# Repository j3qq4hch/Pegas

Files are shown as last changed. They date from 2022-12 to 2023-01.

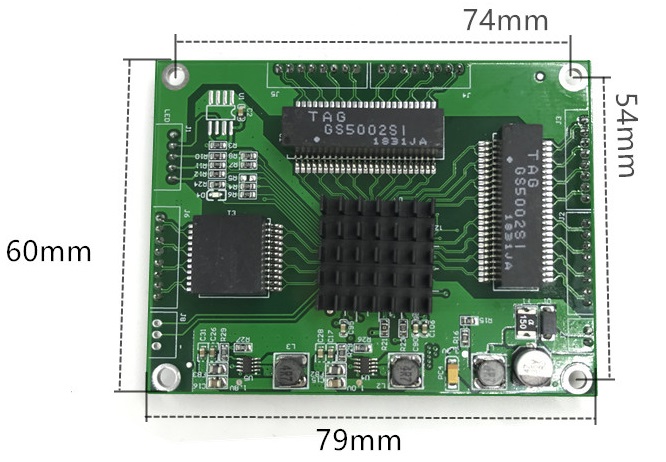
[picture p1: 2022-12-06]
figures/hub5port.jpg

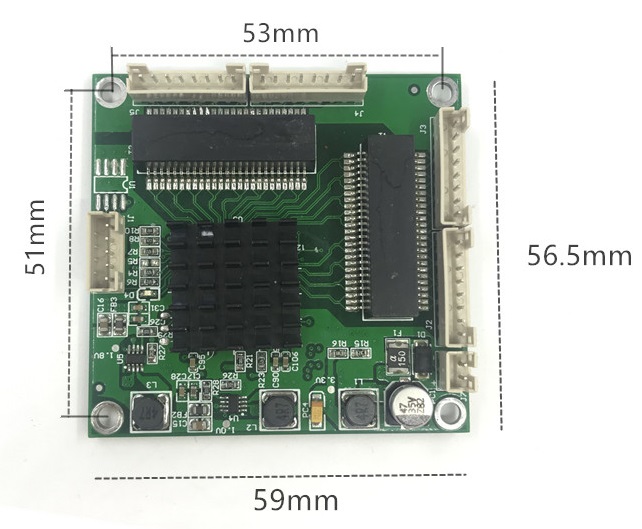
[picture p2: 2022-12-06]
figures/hub4port.jpg

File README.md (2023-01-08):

# Материнская плата БПЛА Pegas

Данный репозиторий содержит документацию и исходные файлы печатных плат электроники БПЛА Пегас.
Набортная электроника представляет собой главным образом материнскую плату (одну или набор из двух), которая служит для распределения питания внутри дрона, а также предоставляет интерфейс для подключения внешних устройств к автопилоту (удобные в производстве и использовании разъемы в удобных местах). БПЛА Пегас использует PX4-совместимый автопилот Cube Orange, которому всегда требуется некая материнская плата (carrier board в репозитории самого автопилота), т.к. он подключается ко всем внешним устройствам разъемом Hirose DF17(1.0H)-80DP-0.5V(57).

Было спроектировано несколько итераций электроники БПЛА Пегас.
## V1 
Самая первая версия устройства, состоящая из одной четырехслойной печатной платы.
Было произведен только один прототип, после чего была спроектирована следующая версия.

## V2
Минимальные отличия от V1, в частности: иная ориентация Cube Orange на плате (он повернут на 60 градусов), что было вызвано багом с устновлением нулевого положения встроенного компаса в ПО PX4, также добавлена схема выключения устройства на N-канальных полевых транзисторах. Схема выключения в этой версии неработоспособна и никогда не была исправлена. 

Также эта версия может быть дополнена внешним ethernet-роутером, который монтируется внутри фюзеляжа БПЛА на специальном кронштейне.

Было спроектировано две платы переходника для покупных модулей роутеров:

Было произведено несколько плат (до 10), которые используются в первых коммерческих аппаратах.

## V3
Полностью переработанная версия электроники: одна четырехслойная материнская плата  заменена на две двухслойные, соединенные мезонинным способом. Снизу располагается силовая плата, на которой размещаются разъемы для подключения моторов, медные полигоны распреления силового питания, DC-DC преобразователи всех вторичных линий питания, а также схема выключения на N-канальных полевых транзисторах. Сверху располагается плата логики с автопилотом и всеми разъемами для подключения внешних устройств. В этой версии произошел переход с миниатюрных разъемов серии JST-GH (как в UAVCAN) на несколько более крупные и значительно более удобные и надежные разъемы JST-XA с защелкой. 

Этот вариант материнской платы предназначен для сборки СЫЧ-версии Пегаса, поэтому помимо типичных компонентов на плате логики также располагается располагается покупной модуль ethernet-концентратора (ссылка тут) и модем телеметрии, поставляемый заказчиком (картинка тут).

Эта версия электроники никогда не была произведена и послужила основой для версии 3.1.

## V3.1

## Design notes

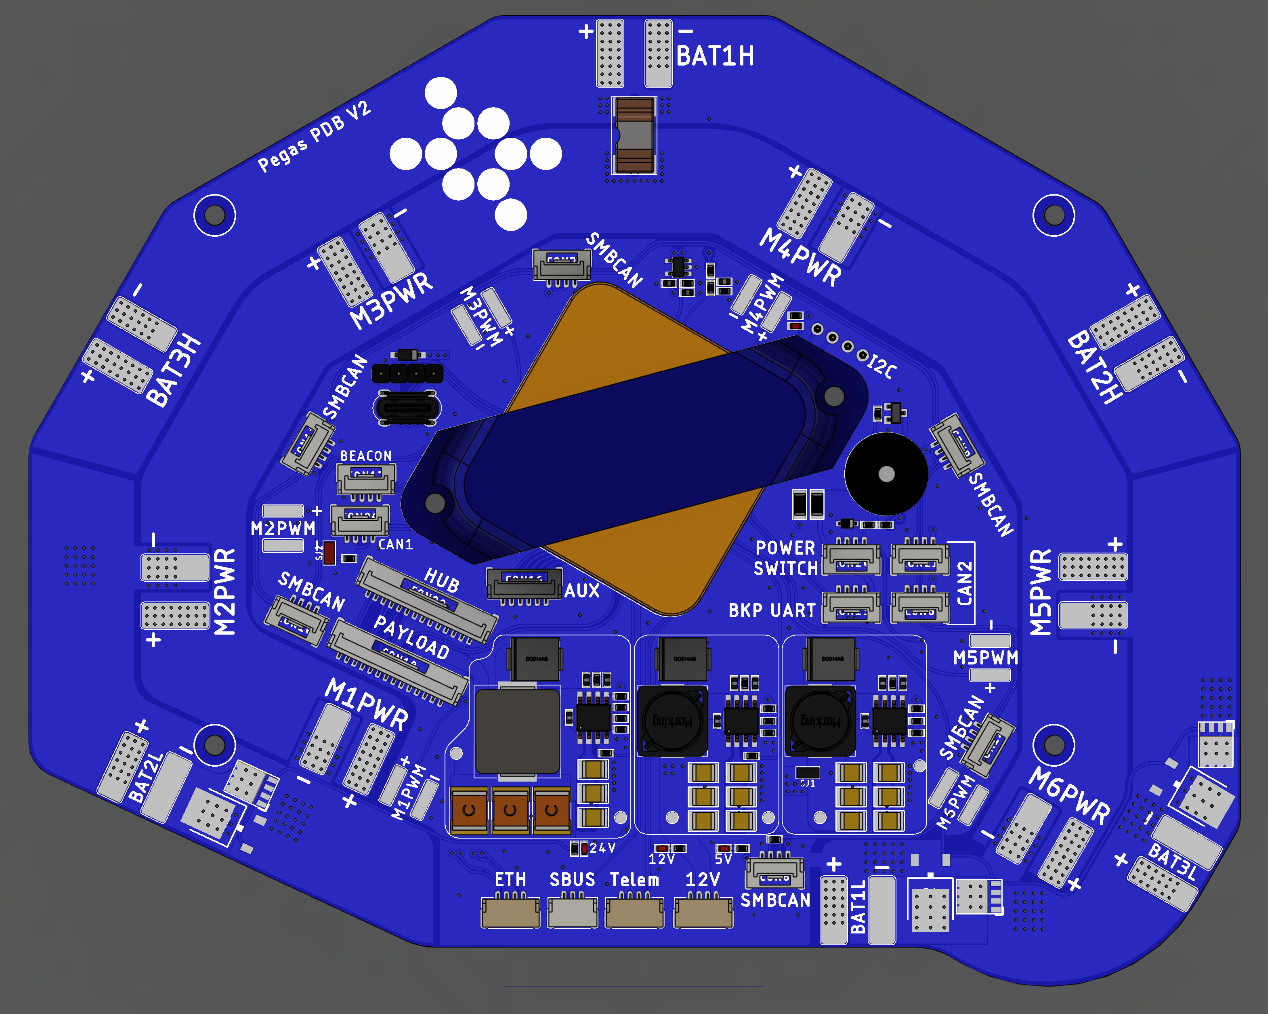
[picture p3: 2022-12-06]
figures/overview.png

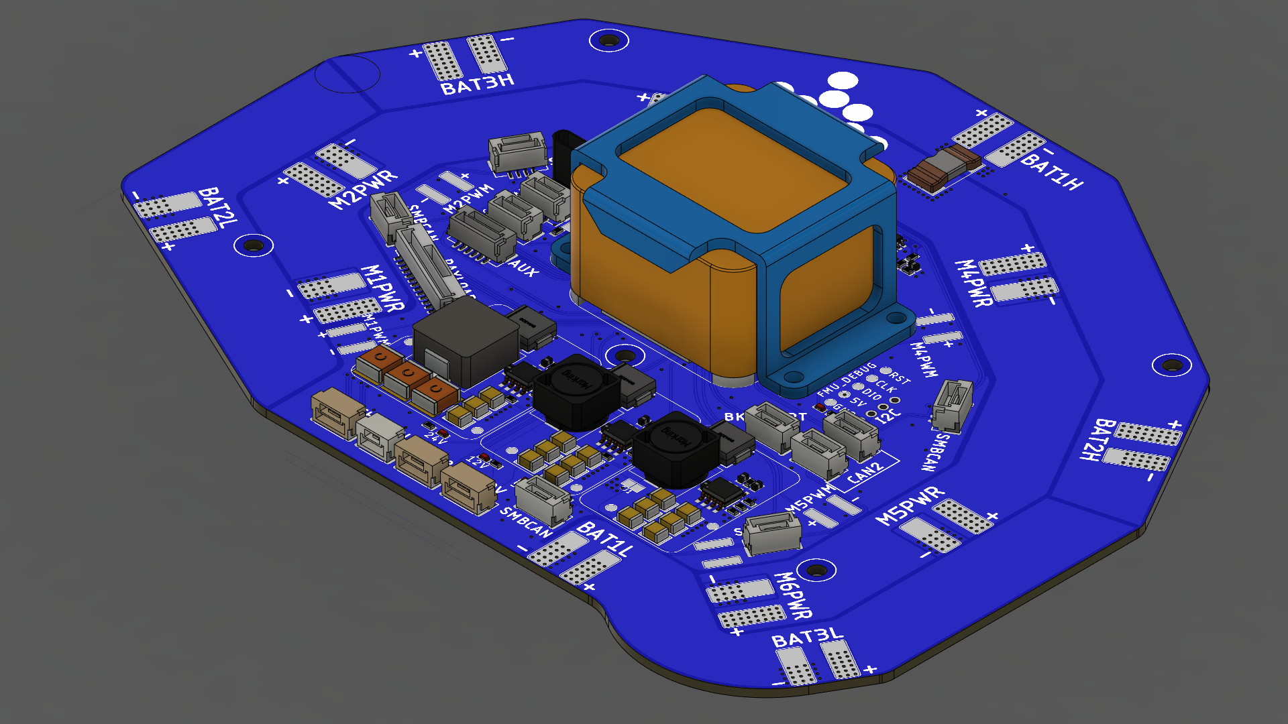
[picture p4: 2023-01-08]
figures/V1_overview.png

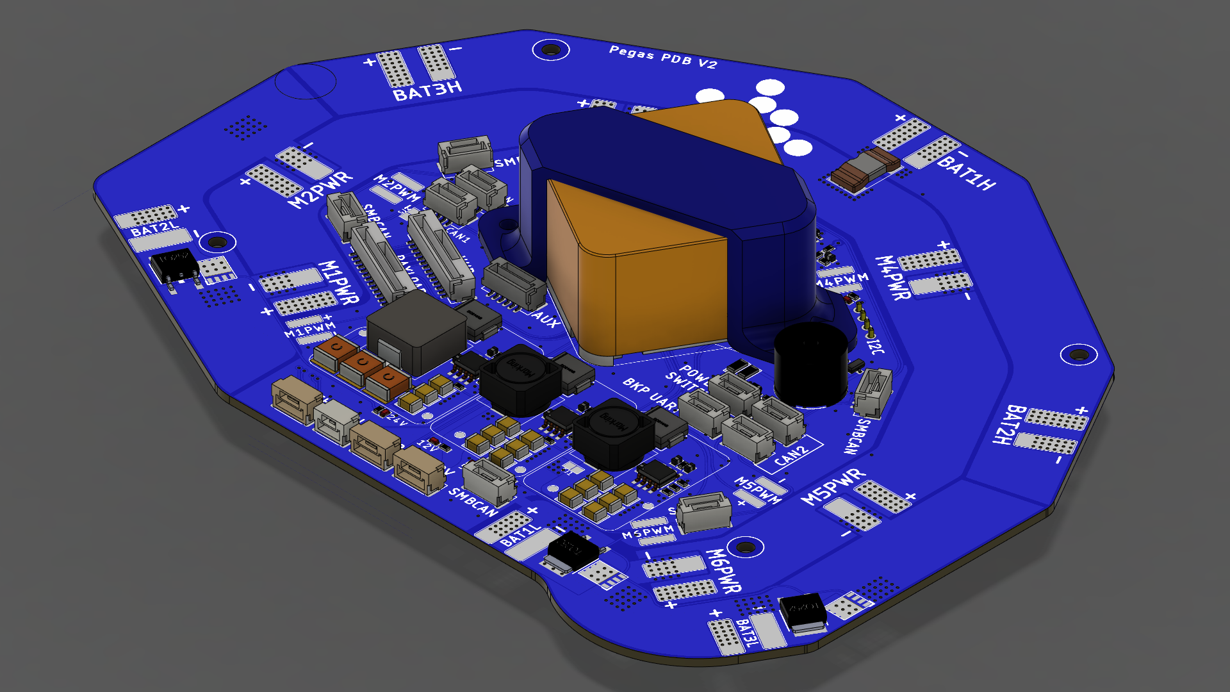
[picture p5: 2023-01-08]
figures/V2_overview.png

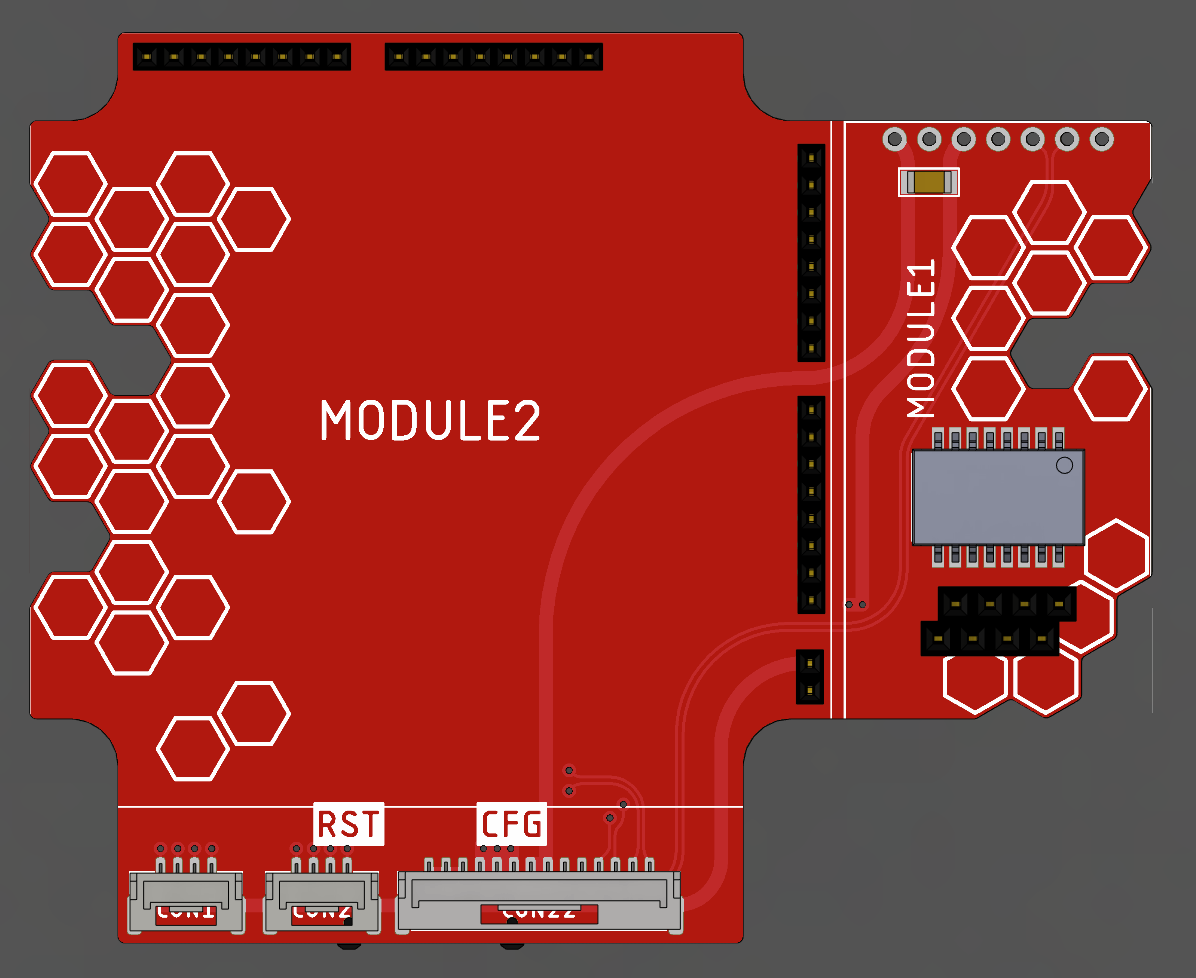
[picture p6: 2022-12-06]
figures/Hub4port_top.png

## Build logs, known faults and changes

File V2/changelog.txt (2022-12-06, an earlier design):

-Исправлено посадочное место USB разъема 
-Исправлена шелкография подключения ШИМ сигнала мотора 6
-Пин VDD_BRICK_VALID подключен к земле
-Полетный контроллер развернут на 60 градусов по часовой стрелки из-за несовершенства ПО PX4
-Изменено расположение последовательных интерфейсов(SERIAL1->CON4, SERIAL5->CON13, SERIAL5->CON17)
-Добавлен разъем для платы хаба

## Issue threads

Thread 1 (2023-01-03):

Ошибки BOM листа релиза 3.1

airPixel, 2023-01-03:
в релизном боме платы логики не попало все что стоит под свитчем, т.е. трансформаторы, дсдс и его обвязка, HLK-7788A

j3qq4hch, 2023-01-03:
Это не ошибка, это вариант сборки СЫЧ. Нельзя устанавливать эти трансформаторы если используется отдельный модуль свитча

airPixel, 2023-01-03:
а, ну ок. просто сижу собираю заказ в элитане и увидел несостыковку. дсдс получается не нужен для свитча?

j3qq4hch, 2023-01-03:
На плате свитча есть свой собственный. Наш не нужен

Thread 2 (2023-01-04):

замены компонентов

airPixel, 2023-01-04:
L1 powerPCB - IHLP2020BZER3R3M01 на VLC5045T-3R3N
вроде подходит и есть в бОльшем колве на элтитане

j3qq4hch, 2023-01-04:
Давай-ка лучше обсуждать замены компонентов из-за доступности не здесь, я не хочу менять их в проекте. Зато мы можем добавить альтернативные колонки в BOM и там же в комментариях это обсудить, если требуется.

airPixel, 2023-01-04:
давай тогда делать BOM всегда в гуглодоках( в этот раз только табличка была в экселе), и там тогда отдельный столбец с заменой. вполне вариант) только нужны права на изменения этого столбца

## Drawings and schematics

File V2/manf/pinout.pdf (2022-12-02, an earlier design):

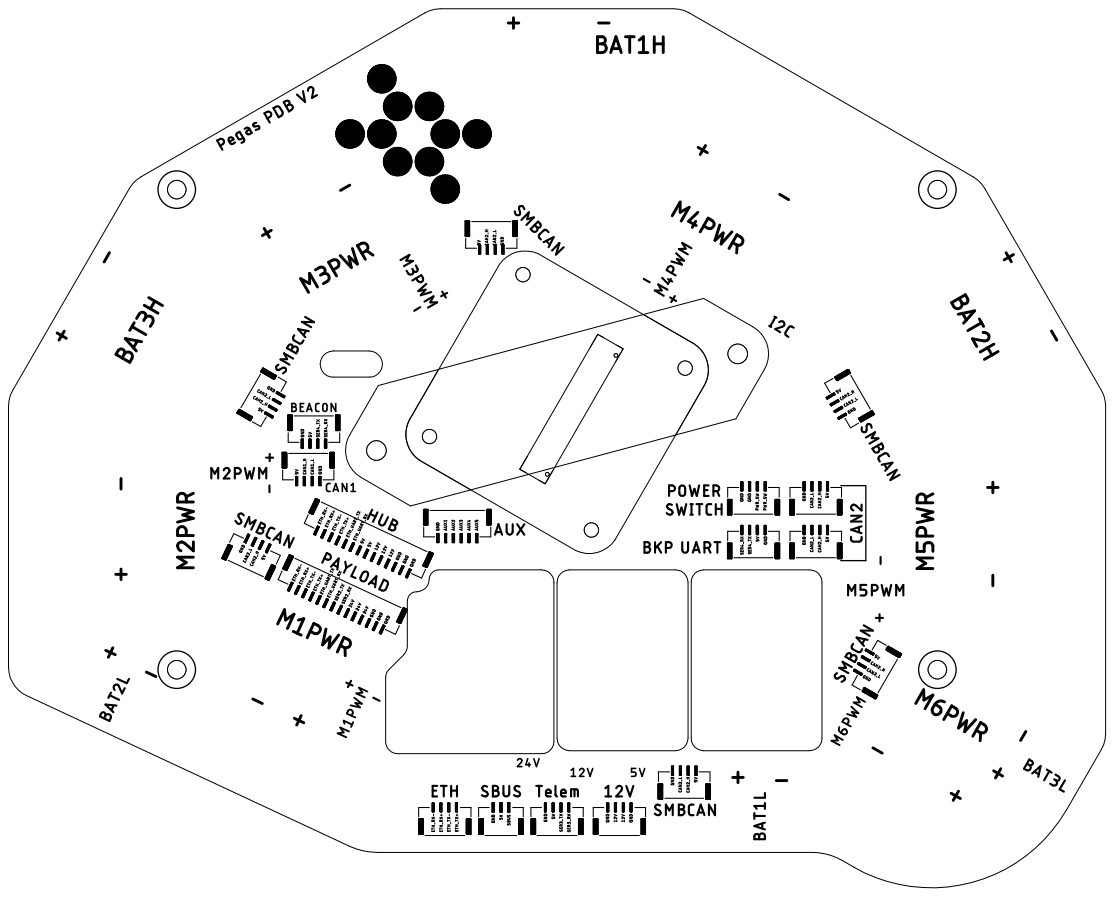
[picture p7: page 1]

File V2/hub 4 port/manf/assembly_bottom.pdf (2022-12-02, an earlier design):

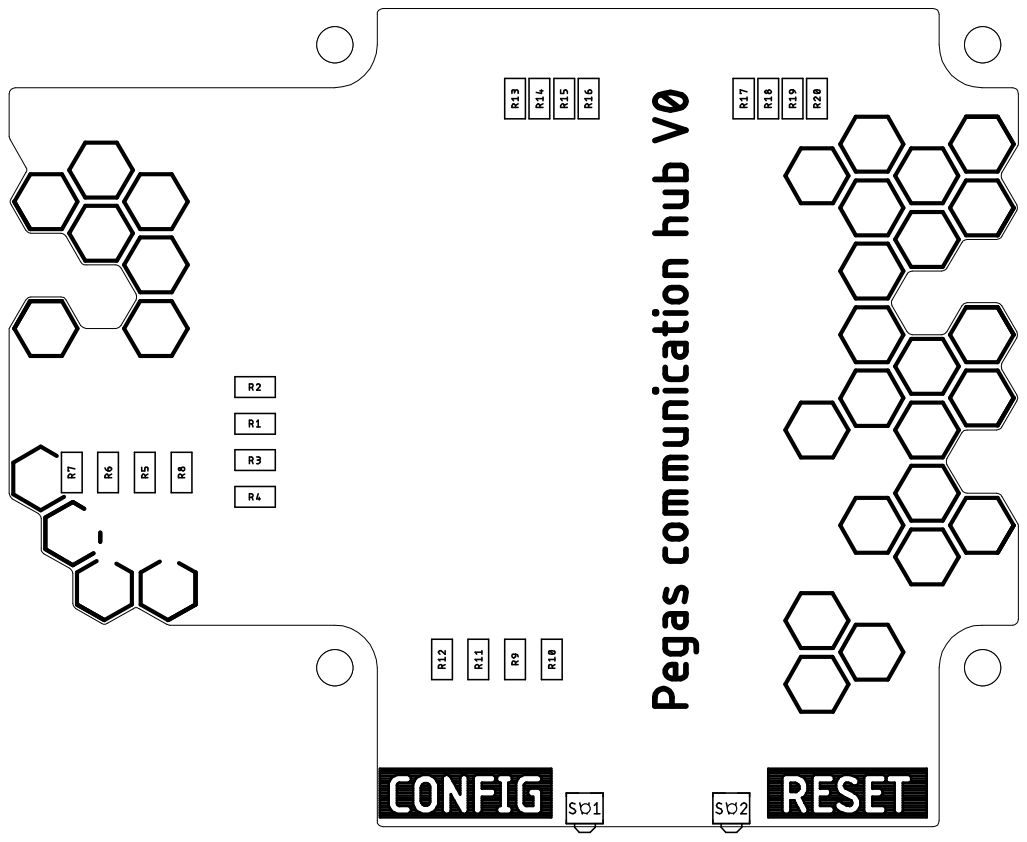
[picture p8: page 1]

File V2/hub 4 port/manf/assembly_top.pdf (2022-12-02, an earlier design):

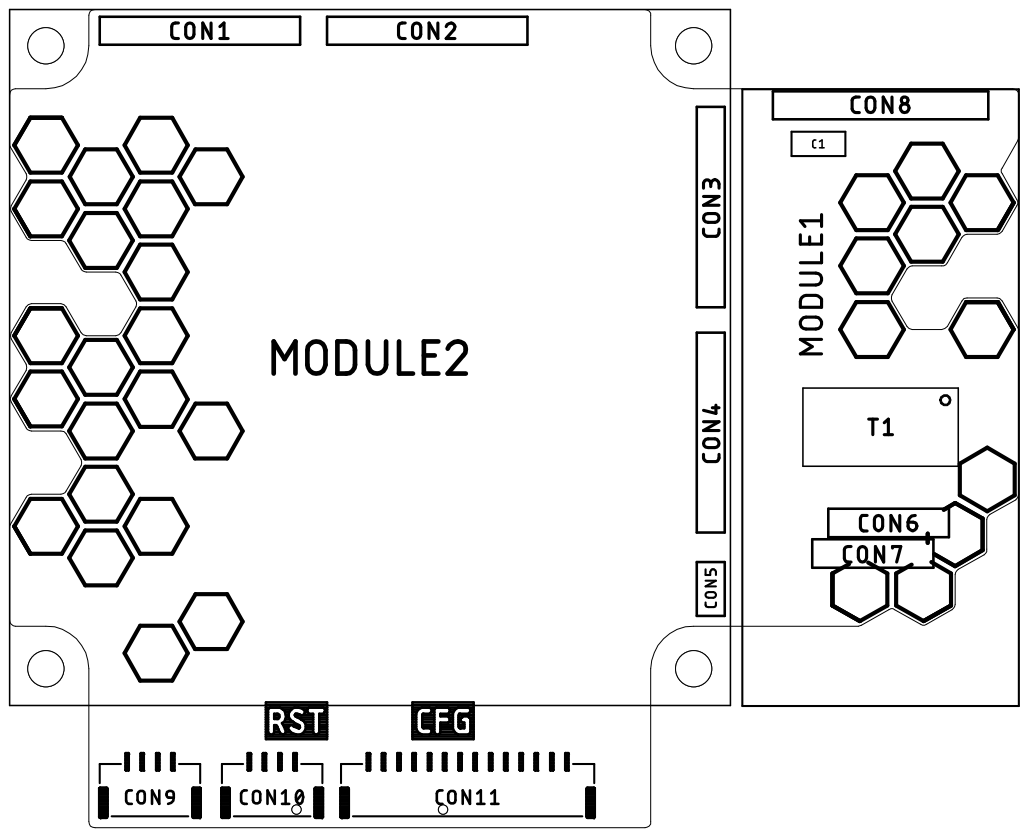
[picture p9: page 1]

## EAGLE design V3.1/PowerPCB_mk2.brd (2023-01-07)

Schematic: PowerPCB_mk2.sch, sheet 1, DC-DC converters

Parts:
C1, C10, C16, C25, C39, C58: 0.1u; C0603; VOLTAGE 50V; LCSC# C14663
C2, C3, C4, C11, C12, C13, C17, C18, C19, C26, C27, C33, C44, C54: 2.2u; C1206; VOLTAGE 100V; LCSC# C170101
C5, C14, C20, C34, C45, C62, C88: 4700p; C0603; VOLTAGE 50V; LCSC# C106218
C6, C15, C21, C35, C87: 47p; C0603; VOLTAGE 50V; LCSC# C1671
C7, C8, C9, C22, C23, C24, C36, C37, C38, C43, C56, C57: 47u; C1206; VOLTAGE 25V; LCSC# C403725
C28, C29, C30, C31, C32, C42: 10u; C1210; VOLTAGE 50V; LCSC# C77102
C40, C41: DNP; C0603
CON1: PINHEAD_1X12-2.54-FEMALE; 1X12-PTH-2.54-FEMALE
CON2, CON4, CON7: PINHEAD_1X06-2.54-FEMALE; 1X06-PTH-2.54-FEMALE
CON3: PINHEAD_1X02-2.54-FEMALE; 1X02-PTH-2.54-FEMALE
D1, D2, D3, D4, D10: B560C; DO-214AB(SMC)
IC1, IC2, IC3, IC4: TPS54560B; SOIC8-POWERPAD
IC5: INA169; SOT23-5
IC10: TPS54260; MSOP10; DIGIKEY# 296-28183-1-ND
J1: CONNECTION-7MM; CONNECTION_7MM
L1: 3.3uH; IHLP-2020BZ-01; LCSC# C844988
L2, L4, L5: 7.2uH; 1064
L3: 22µH; SRP1265A
Q1: IRLML9301; SOT23
R1, R5, R9, R13: 243K; R0603; LCSC# C23351
R2, R6, R10, R14, R22, R29: 18K; R0603; LCSC# C25810
R3, R11: 53K6; R0603; LCSC# C23074
R4, R8, R12, R16, R17, R20, R23, R28: 10K; R0603; LCSC# C160601
R7, R15, R21, R25: 143K; R0603; LCSC# C22877
R18, R26: 700 µOhms; R3920-KELVIN
R27: 39K; R0603; LCSC# C23153
RL: 53K6; R0603; LCSC# C23074
RL1: DNM; R0603; LCSC# C23153

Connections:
5VFMU: C7.P$2 (2), C8.P$2 (2), C9.P$2 (2), C39.2, IC5.5 (V+), L2.2, Q1.2 (S), R3.2, R23.1; also elsewhere on the board
5V_FMU_CTRL: Q1.1 (G), R23.2
BATNEG: CON3.1
BATT_CURRENT: C40.2, CON1.12, IC5.1 (OUT), RL.2, RL1.2
BATT_VOLTAGE: C41.2, CON1.11, R20.2, R22.1
BOOT: C58.2, IC10.1 (BOOT)
BOOT1: C1.1, IC1.1 (BOOT)
BOOT2: C16.1, IC3.1 (BOOT)
BOOT3: C25.1, IC4.1 (BOOT)
DC-DC_EN: IC2.3 (EN), IC3.3 (EN), IC4.3 (EN), IC10.3 (EN); also elsewhere on the board
GND: C2.P$1 (1), C3.P$1 (1), C4.P$1 (1), C5.1, C6.1, C7.P$1 (1), C8.P$1 (1), C9.P$1 (1), C11.P$1 (1), C12.P$1 (1), C13.P$1 (1), C14.1, C15.1, C17.P$1 (1), C18.P$1 (1), C19.P$1 (1), C20.1, C21.1, C22.P$1 (1), C23.P$1 (1), C24.P$1 (1), C26.P$1 (1), C27.P$1 (1), C28.1, C29.1, C30.1, C31.1, C32.1, C33.P$1 (1), C34.1, C35.1, C36.P$1 (1), C37.P$1 (1), C38.P$1 (1), C39.1, C40.1, C41.1, C42.1, C43.P$2 (2), C44.P$1 (1), C45.2, C54.P$1 (1), C56.P$2 (2), C57.P$2 (2), C62.2, C87.2, C88.2, CON1.1, CON1.2, CON1.5, CON1.6, CON1.7, CON2.1, CON2.2, CON2.3, CON4.4, CON4.5, CON4.6, CON7.4, CON7.5, CON7.6, D1.A, D2.A, D3.A, D4.A, D10.A, IC1.7 (GND), IC1.P$1 (GND), IC2.7 (GND), IC2.P$1 (GND), IC3.7 (GND), IC3.P$1 (GND), IC4.7 (GND), IC4.P$1 (GND), IC5.2 (GND), IC10.9 (GND), IC10.EP (GND), J1.2, R1.1, R4.1, R5.1, R8.1, R9.1, R12.1, R13.1, R16.1, R17.1, R20.1, R25.1, R28.1, RL.1, RL1.1; also elsewhere on the board
unnamed: IC1.4 (RT/CLK), R1.2
unnamed: IC3.4 (RT/CLK), R9.2
unnamed: C6.2, IC1.6 (COMP), R2.2
unnamed: C5.2, R2.1
unnamed: IC1.5 (FB), R3.1, R4.2
unnamed: C21.2, IC3.6 (COMP), R10.2
unnamed: C10.1, IC2.1 (BOOT)
unnamed: C10.2, D2.C, IC2.8 (SW), L3.1
unnamed: IC2.4 (RT/CLK), R5.2
unnamed: C15.2, IC2.6 (COMP), R6.2
unnamed: C14.2, R6.1
unnamed: IC2.5 (FB), R7.1, R8.2, R17.2
unnamed: C20.2, R10.1
unnamed: IC4.4 (RT/CLK), R13.2
unnamed: IC3.5 (FB), R11.1, R12.2
unnamed: C35.2, IC4.6 (COMP), R14.2
unnamed: C34.2, R14.1
unnamed: IC4.5 (FB), R15.1, R16.2
unnamed: IC5.4 (VIN-), R18.S2, R26.S2
unnamed: C45.1, C62.1, IC10.4 (SS/TR)
unnamed: IC5.3 (VIN+), R18.S1, R26.S1
unnamed: R21.1, R22.2
unnamed: CON1.8, CON1.9, CON1.10, Q1.3 (D)
unnamed: C87.1, IC10.8 (COMP), R29.2
unnamed: IC10.5 (RT/CLK), R25.2
unnamed: C88.1, R29.1
PGND: J1.1; also elsewhere on the board
PH: C58.1, D10.C, IC10.10 (PH), L1.P$1 (1)
PWRSW: CON3.2
SW1: C1.2, D1.C, IC1.8 (SW), L2.1
SW2: C16.2, D3.C, IC3.8 (SW), L4.1
SW3: C25.2, D4.C, IC4.8 (SW), L5.1
VBAT: C2.P$2 (2), C3.P$2 (2), C4.P$2 (2), C11.P$2 (2), C12.P$2 (2), C13.P$2 (2), C17.P$2 (2), C18.P$2 (2), C19.P$2 (2), C26.P$2 (2), C27.P$2 (2), C33.P$2 (2), C44.P$2 (2), C54.P$2 (2), IC1.2 (VIN), IC2.2 (VIN), IC3.2 (VIN), IC4.2 (VIN), IC10.2 (VIN), R18.2, R18.22 (2), R21.2, R26.2, R26.22 (2); also elsewhere on the board
VDC: R18.1, R18.11 (1), R26.1, R26.11 (1); also elsewhere on the board
VDD_4V: C43.P$1 (1), C56.P$1 (1), C57.P$1 (1), CON1.3, CON1.4, L1.P$2 (2), R27.2
VDD_5V: C22.P$2 (2), C23.P$2 (2), C24.P$2 (2), CON4.1, CON4.2, CON4.3, L4.2, R11.2
VDD_12V: C36.P$2 (2), C37.P$2 (2), C38.P$2 (2), CON7.1, CON7.2, CON7.3, L5.2, R15.2
VDD_24V: C28.2, C29.2, C30.2, C31.2, C32.2, C42.2, CON2.4, CON2.5, CON2.6, L3.2, R7.2
VSENSE: IC10.7 (VSENSE), R27.1, R28.2

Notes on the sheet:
24V power source
5V power source
When EN is left floating TPS54560 is enabled
12V power source
EN - Enable terminal, with internal pull-up current source. Pull below 1.2 V to disable. Float to enable.
EN PIN: Pull below 1.2 V to disable. Float to enable.
143K on RT/CLK is for ~800 KHz switching frequency
TPS54560/54260 Vout = 0.8 * (Rh/Rl + 1)
Vout = 3,92 V
Vout = 23,68 V
Vout = 12,24 V
Vout = 5.088
Place C3 in case low pass filtering on the output needed
For most applications, best performance is attained with an RS value that provides a full-scale shunt voltage of 50 mV to 100 mV; maximum input voltage for accurate measurements is 500 mV.
Imax = 169 A Vout max = 3.17 V

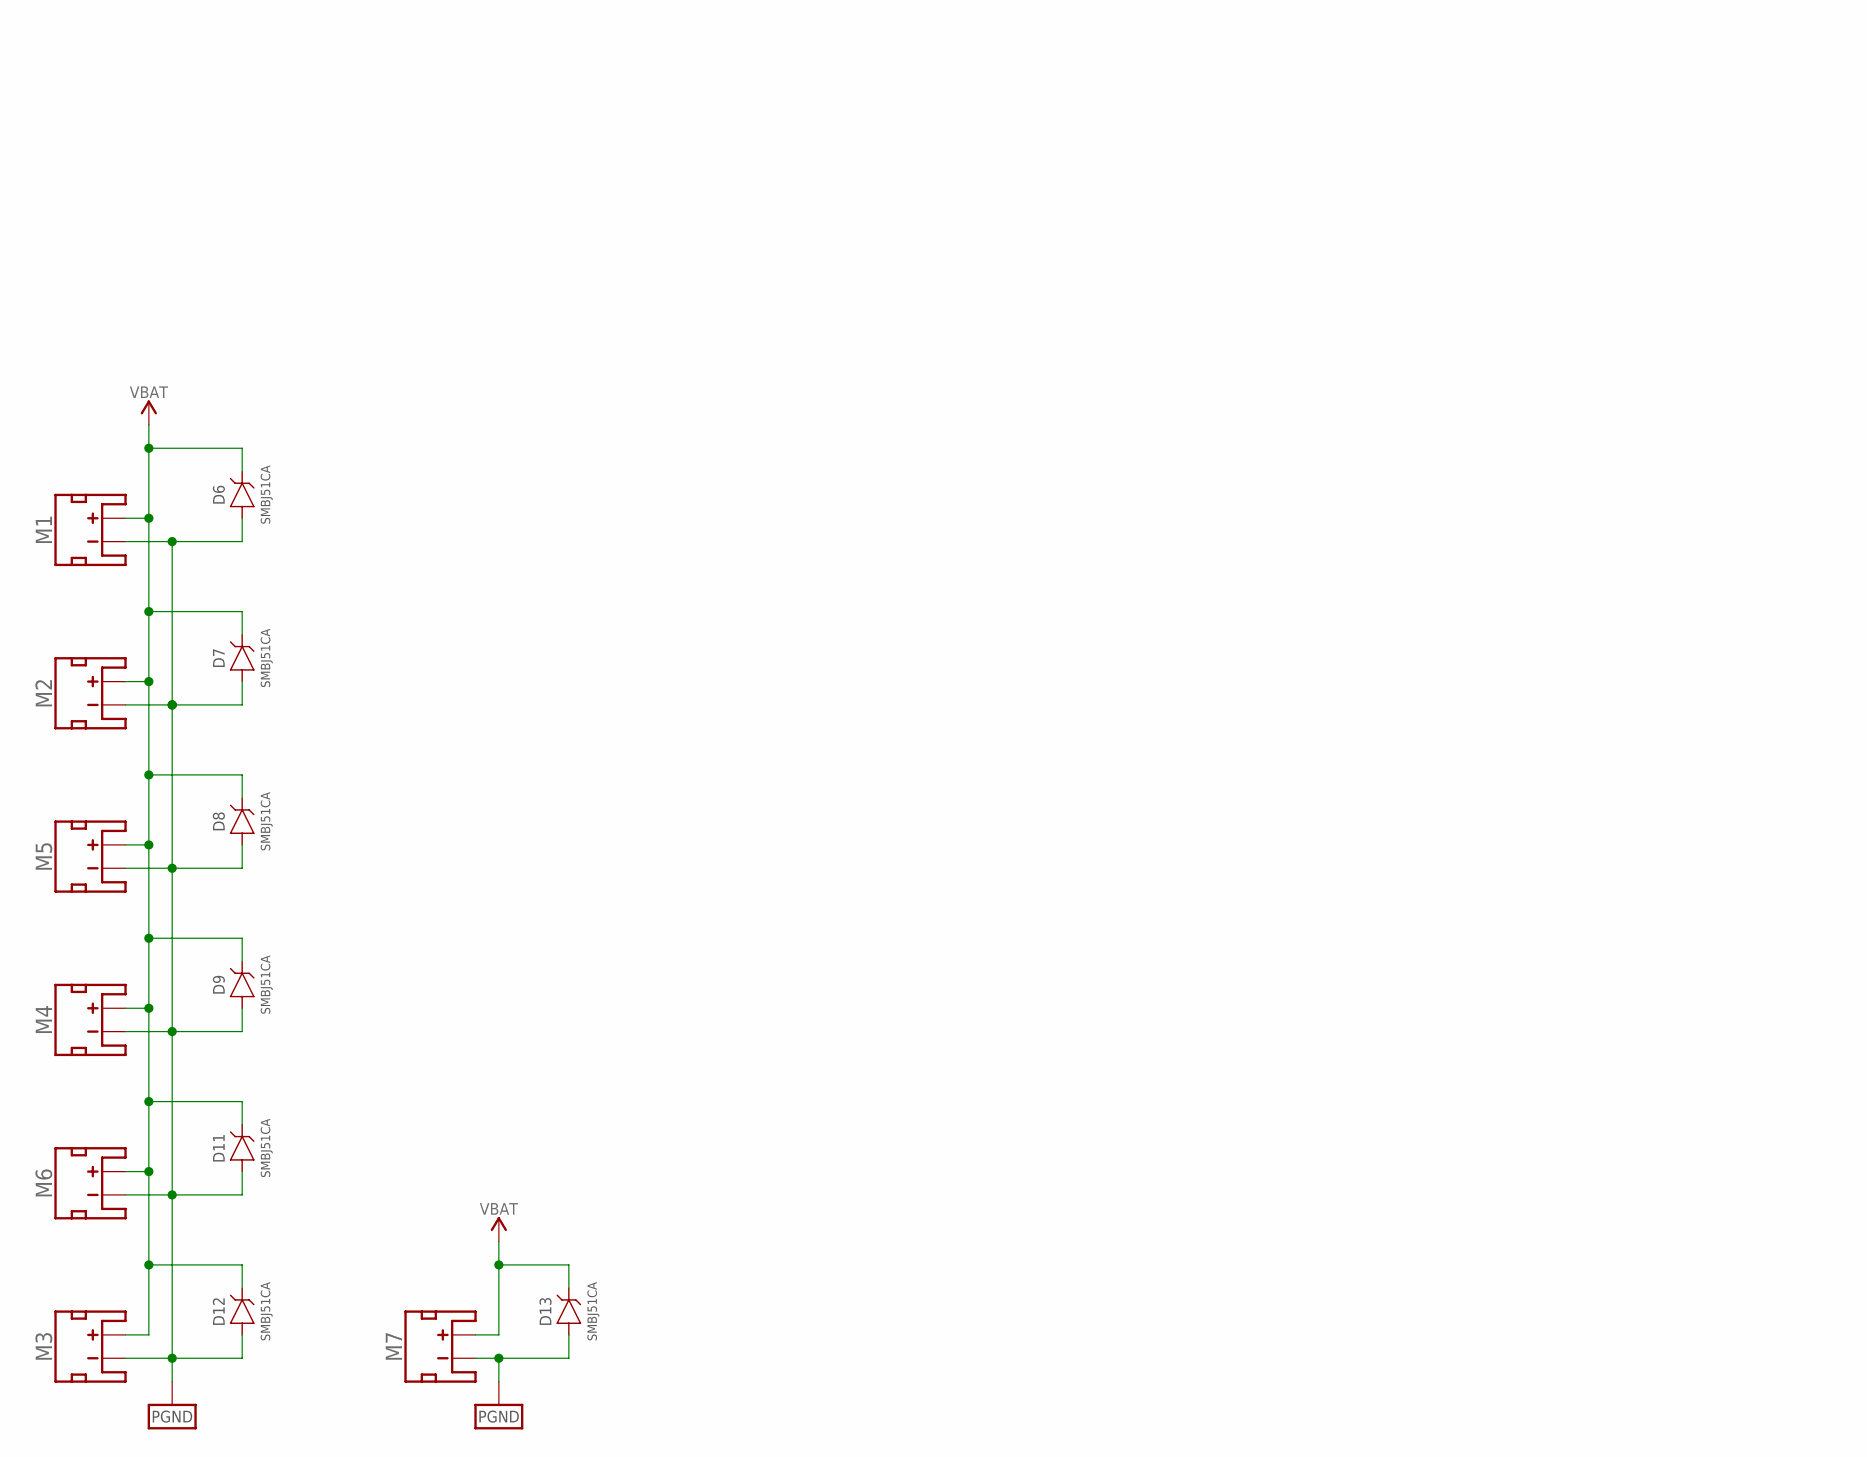
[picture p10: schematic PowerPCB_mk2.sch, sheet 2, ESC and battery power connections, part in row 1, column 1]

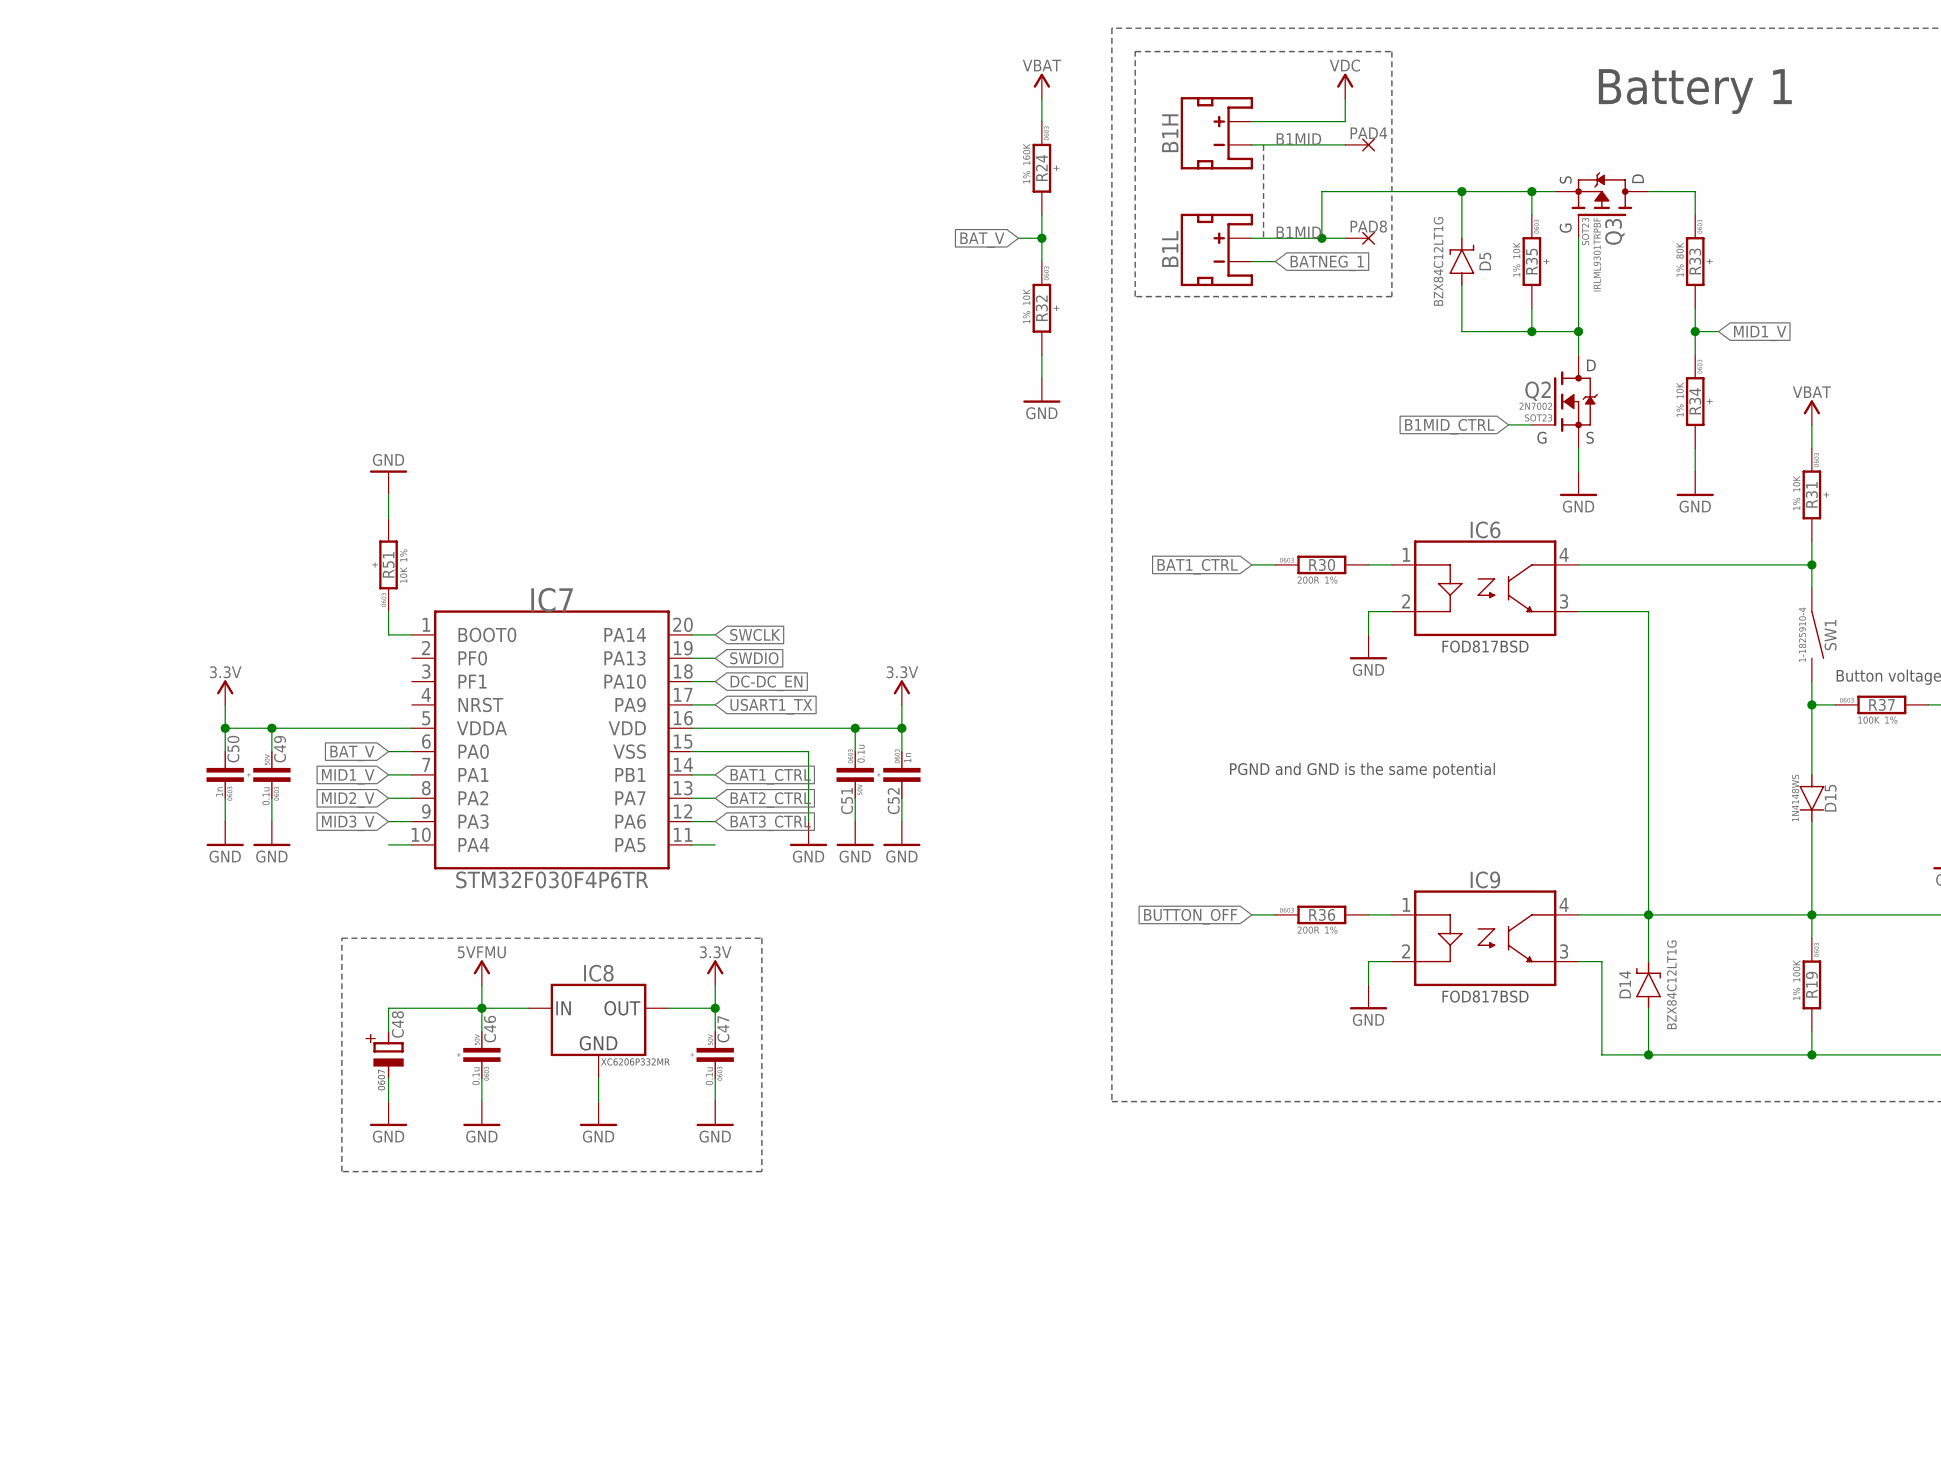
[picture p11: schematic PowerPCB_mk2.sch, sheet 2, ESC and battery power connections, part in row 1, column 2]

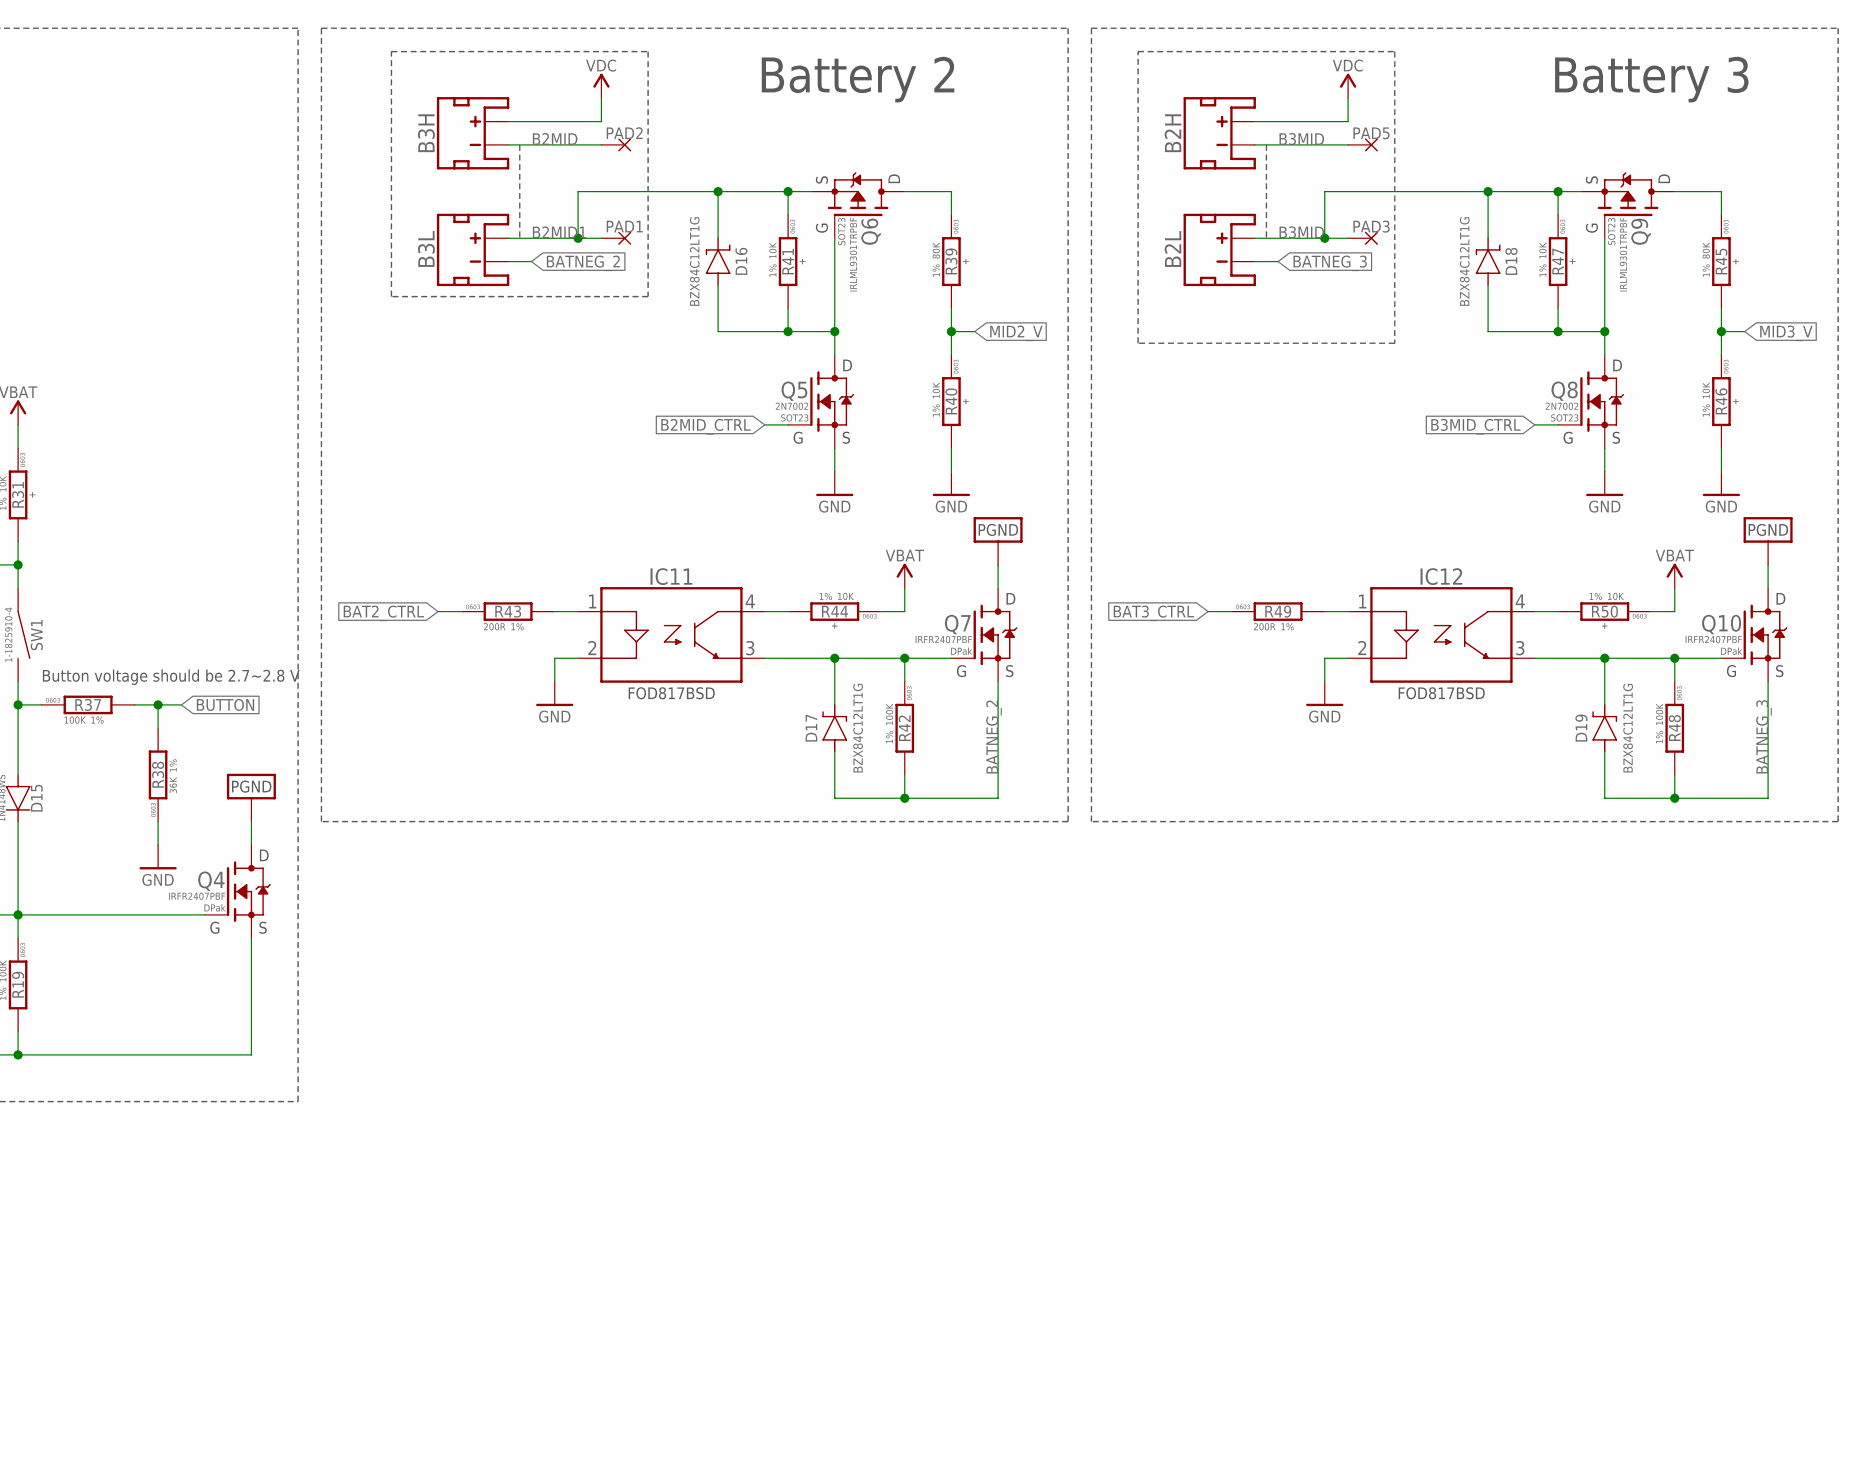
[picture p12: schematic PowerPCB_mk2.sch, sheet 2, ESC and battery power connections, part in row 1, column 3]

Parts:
B1H, B1L, B2H, B2L, B3H, B3L: BATTERY_CON-XT60PW-M; XT60PW-M
C46, C47, C49, C51: 0.1u; C0603; VOLTAGE 50V; LCSC# C14663
C48: CPOL-SMD_6.3X7.7; CAP_SMD_6.3X7.7
C50, C52: 1n; C0603
D5, D14, D16, D17, D18, D19: BZX84C12; SOT23
D6, D7, D8, D9, D11, D12, D13: SMBJ51CA-SMB; DO-214AA(SMB)
D15: 1N4148WS; SOD323
IC6, IC9, IC11, IC12: FOD817; 4-SMD
IC7: STM32F030F4P6; TSSOP20
IC8: XC6206P332MR; SOT23
M1, M2, M3, M4, M5, M6, M7: BATTERY_CON-XT30-RA; XT30-RA
PAD1, PAD2, PAD3, PAD4, PAD5, PAD8: PAD-10X4; 10X4
Q2, Q5, Q8: 2N7002; SOT23
Q3, Q6, Q9: IRLML9301; SOT23
Q4, Q7, Q10: IRFR2407PBF; D-PAK
R19, R37, R42, R48: 100K; R0603
R24: 160K; R0603; LCSC# C160601
R30, R36, R43, R49: 200R; R0603
R31, R32, R34, R35, R40, R41, R44, R46, R47, R50, R51: 10K; R0603; LCSC# C160601
R33, R39, R45: 80K; R0603; LCSC# C160601
R38: 36K; R0603
SW1: TACT_SWITCH-1-1825910-4; 1-1825910-4

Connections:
5VFMU: C46.2, C48.+, IC8.3 (IN); also elsewhere on the board
B1MID: B1H.-, B1L.+, D5.3 (C), PAD4.P$1, PAD8.P$1, Q3.2 (S), R35.1
B1MID_CTRL: Q2.1 (G)
B2MID: B3H.-, PAD2.P$1
B2MID1: B3L.+, D16.3 (C), PAD1.P$1, Q6.2 (S), R41.1
B2MID_CTRL: Q5.1 (G)
B3MID: B2H.-, B2L.+, D18.3 (C), PAD3.P$1, PAD5.P$1, Q9.2 (S), R47.1
B3MID_CTRL: Q8.1 (G)
BAT1_CTRL: IC7.14 (PB1), R30.1
BAT2_CTRL: IC7.13 (PA7), R43.1
BAT3_CTRL: IC7.12 (PA6), R49.1
BATNEG_1: B1L.-, D14.1 (A), IC9.3 (EMITTER), Q4.S, R19.2
BATNEG_2: B3L.-, D17.1 (A), Q7.S, R42.2
BATNEG_3: B2L.-, D19.1 (A), Q10.S, R48.2
BAT_V: IC7.6 (PA0), R24.2, R32.1
BUTTON: R37.2, R38.2
BUTTON_OFF: R36.1
DC-DC_EN: IC7.18 (PA10); also elsewhere on the board
GND: C46.1, C47.1, C48.-, C49.1, C50.1, C51.2, C52.2, IC6.2 (C), IC7.15 (VSS), IC8.1 (GND), IC9.2 (C), IC11.2 (C), IC12.2 (C), Q2.2 (S), Q5.2 (S), Q8.2 (S), R32.2, R34.2, R38.1, R40.2, R46.2, R51.2; also elsewhere on the board
MID1_V: IC7.7 (PA1), R33.2, R34.1
MID2_V: IC7.8 (PA2), R39.2, R40.1
MID3_V: IC7.9 (PA3), R45.2, R46.1
unnamed: D14.3 (C), D15.C, IC6.3 (EMITTER), IC9.4 (COLLECTOR), Q4.G, R19.1
unnamed: IC6.1 (A), R30.2
unnamed: IC6.4 (COLLECTOR), R31.2, SW1.1, SW1.2 (1)
unnamed: IC9.1 (A), R36.2
unnamed: D15.A, R37.1, SW1.3 (2), SW1.4 (2)
unnamed: D5.1 (A), Q2.3 (D), Q3.1 (G), R35.2
unnamed: Q3.3 (D), R33.1
unnamed: Q6.3 (D), R39.1
unnamed: D16.1 (A), Q5.3 (D), Q6.1 (G), R41.2
unnamed: IC11.1 (A), R43.2
unnamed: D17.3 (C), IC11.3 (EMITTER), Q7.G, R42.1
unnamed: Q9.3 (D), R45.1
unnamed: IC11.4 (COLLECTOR), R44.2
unnamed: D18.1 (A), Q8.3 (D), Q9.1 (G), R47.2
unnamed: IC12.1 (A), R49.2
unnamed: D19.3 (C), IC12.3 (EMITTER), Q10.G, R48.1
unnamed: IC12.4 (COLLECTOR), R50.2
unnamed: IC7.1 (BOOT0), R51.1
PGND: D6.A, D7.A, D8.A, D9.A, D11.A, D12.A, D13.A, M1.-, M2.-, M3.-, M4.-, M5.-, M6.-, M7.-, Q4.D, Q7.D, Q10.D; also elsewhere on the board
SWCLK: IC7.20 (PA14)
SWDIO: IC7.19 (PA13)
USART1_TX: IC7.17 (PA9)
VBAT: D6.C, D7.C, D8.C, D9.C, D11.C, D12.C, D13.C, M1.+, M2.+, M3.+, M4.+, M5.+, M6.+, M7.+, R24.1, R31.1, R44.1, R50.1; also elsewhere on the board
VDC: B1H.+, B2H.+, B3H.+; also elsewhere on the board
VDD_3V3: C47.2, C49.2, C50.2, C51.1, C52.1, IC7.5 (VDDA), IC7.16 (VDD), IC8.2 (OUT)

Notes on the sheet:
Battery 1
Battery 2
Button voltage should be 2.7~2.8 V
PGND and GND is the same potential
Battery 3

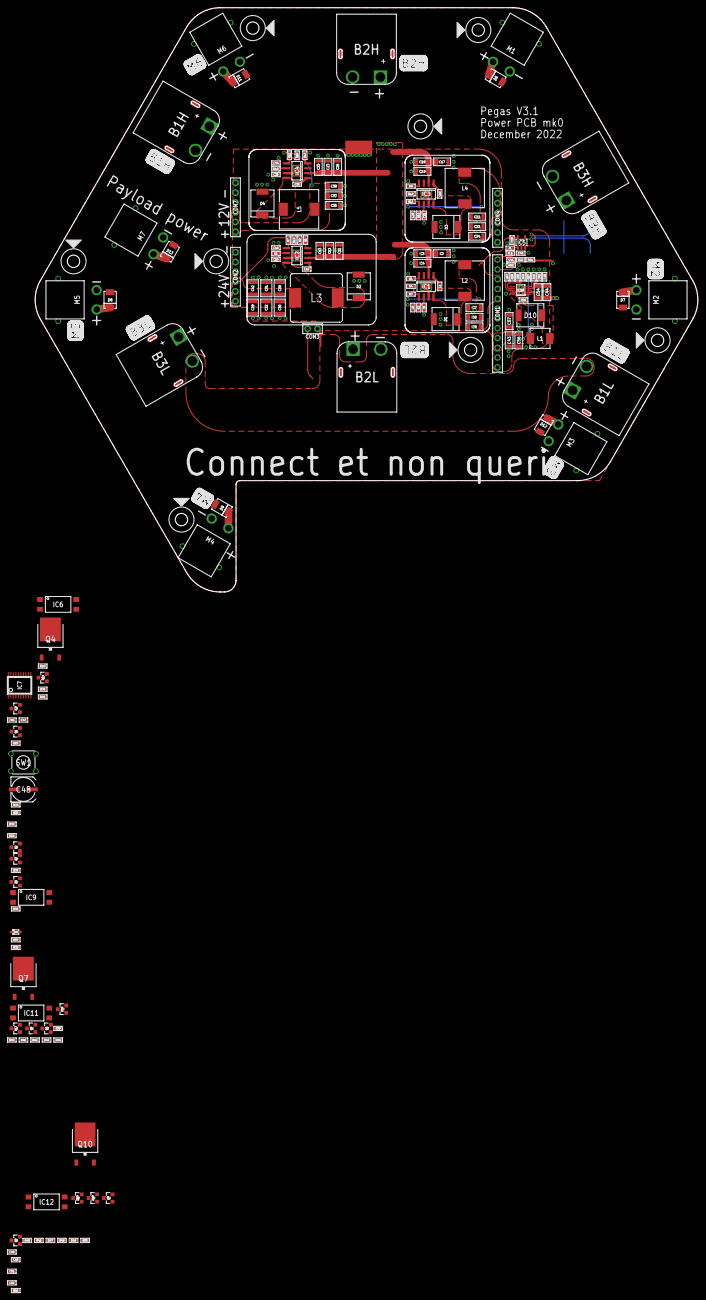
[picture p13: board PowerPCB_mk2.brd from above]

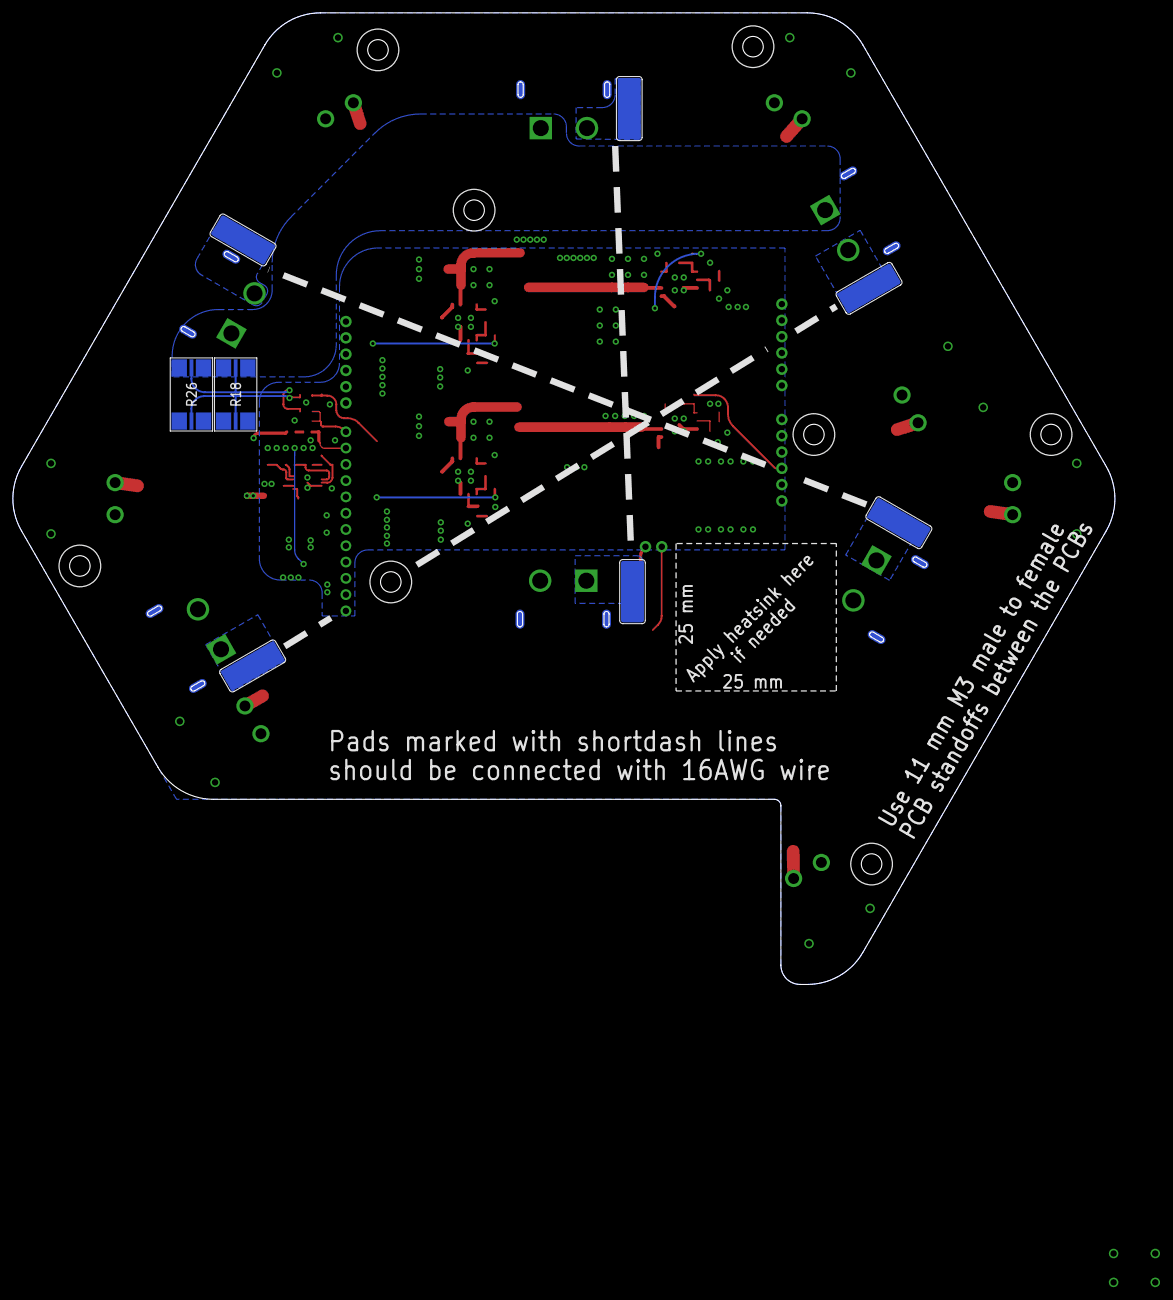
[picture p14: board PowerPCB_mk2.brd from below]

Board: 2 copper layers, 171.9 x 151.6 mm, 184 parts (8 on the bottom side), 82 nets.

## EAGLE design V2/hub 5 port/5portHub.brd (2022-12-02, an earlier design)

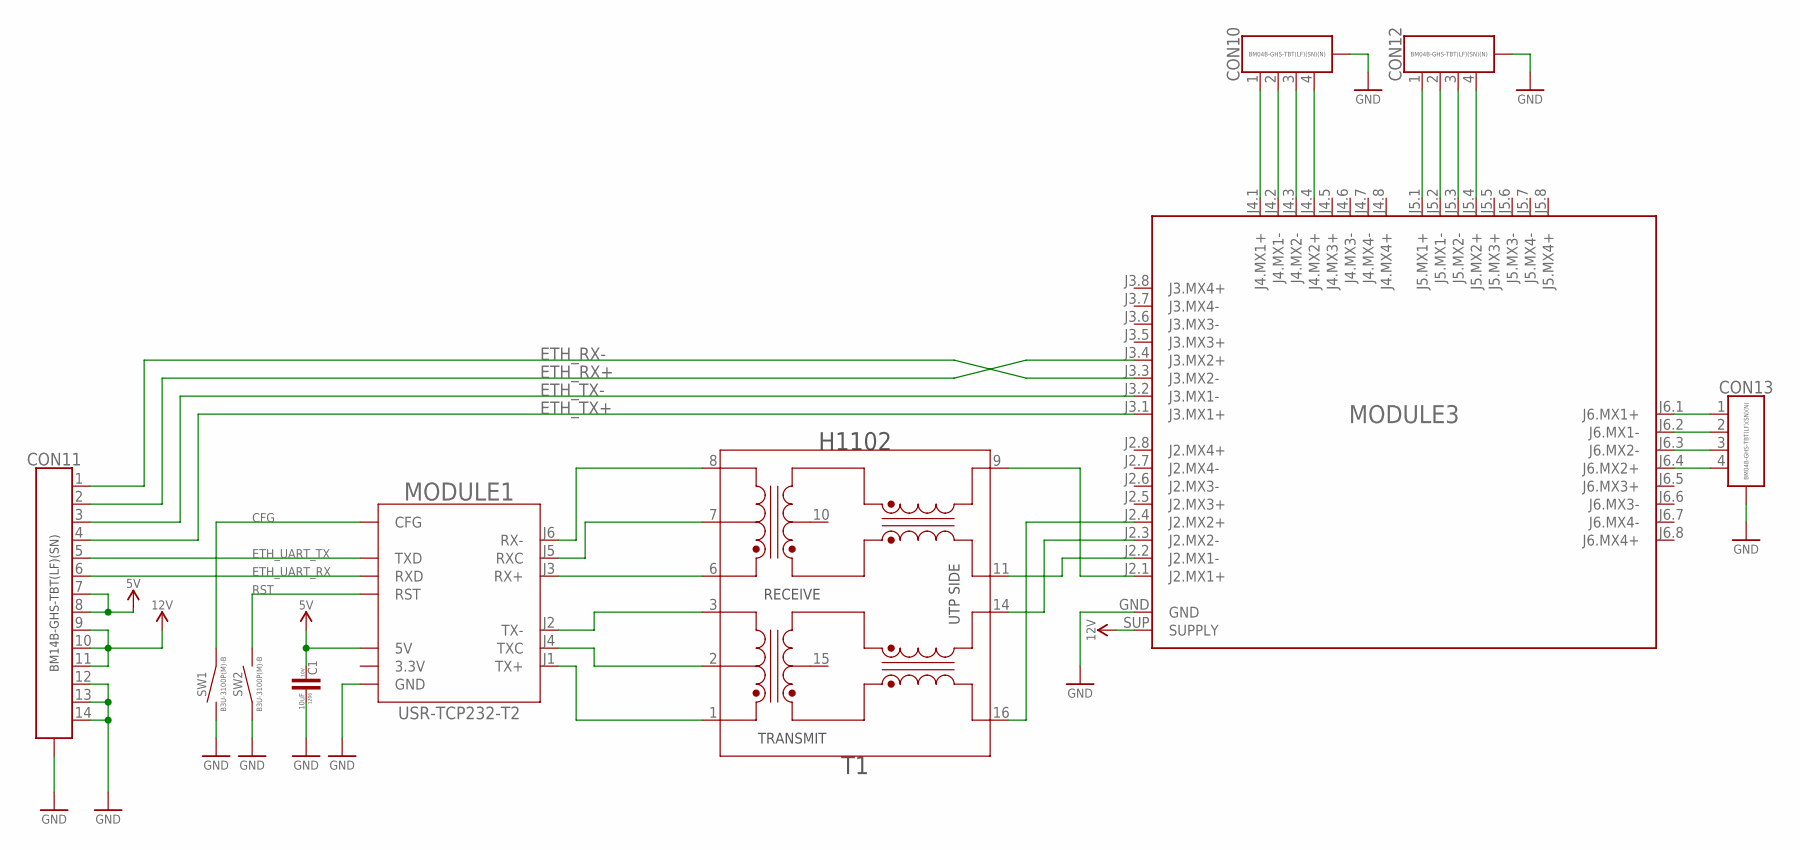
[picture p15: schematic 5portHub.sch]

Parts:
C1: 10uF; C1206; VOLTAGE 10V
CON10, CON12, CON13: CON-4P-TABS-JST-GH-TOP; BM04B-GHS-TB
CON11: CON-14P-TABS-JST-GH-TOP; BM14B-GHS-TBT
MODULE1: USR-TCP232-T2
MODULE3: ANDDEAR_5PORT3
SW1, SW2: TACT_SWITCH-B3U-3100P(M)-B; B3U-3100P(M)-B
T1: H1102NL; H1102

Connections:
CFG: MODULE1.CFG, SW1.P$1 (1)
ETH_RX+: CON11.2, MODULE3.J3.4 (J3.MX2+)
ETH_RX-: CON11.1, MODULE3.J3.3 (J3.MX2-)
ETH_TX+: CON11.4, MODULE3.J3.1 (J3.MX1+)
ETH_TX-: CON11.3, MODULE3.J3.2 (J3.MX1-)
ETH_UART_RX: CON11.6, MODULE1.RXD
ETH_UART_TX: CON11.5, MODULE1.TXD
GND: C1.P$1 (1), CON10.M$0 (GND), CON10.M$1 (GND), CON11.12, CON11.13, CON11.14, CON11.M$0 (G1), CON11.M$1 (G1), CON12.M$0 (GND), CON12.M$1 (GND), CON13.M$0 (GND), CON13.M$1 (GND), MODULE1.GND, MODULE3.GND, SW1.P$2 (2), SW2.P$1 (1)
unnamed: CON13.1, MODULE3.J6.1 (J6.MX1+)
unnamed: CON13.2, MODULE3.J6.2 (J6.MX1-)
unnamed: CON13.3, MODULE3.J6.3 (J6.MX2-)
unnamed: CON13.4, MODULE3.J6.4 (J6.MX2+)
unnamed: MODULE3.J2.1 (J2.MX1+), T1.9
unnamed: MODULE3.J2.2 (J2.MX1-), T1.11
unnamed: MODULE3.J2.3 (J2.MX2-), T1.14
unnamed: MODULE3.J2.4 (J2.MX2+), T1.16
unnamed: MODULE1.J6 (RX-), T1.8
unnamed: MODULE1.J1 (TX+), T1.1
unnamed: MODULE1.J2 (TX-), T1.3
unnamed: MODULE1.J3 (RX+), T1.6
unnamed: CON12.1, MODULE3.J5.1 (J5.MX1+)
unnamed: CON12.2, MODULE3.J5.2 (J5.MX1-)
unnamed: CON12.3, MODULE3.J5.3 (J5.MX2-)
unnamed: CON12.4, MODULE3.J5.4 (J5.MX2+)
unnamed: CON10.1, MODULE3.J4.1 (J4.MX1+)
unnamed: CON10.2, MODULE3.J4.2 (J4.MX1-)
unnamed: CON10.3, MODULE3.J4.3 (J4.MX2-)
unnamed: CON10.4, MODULE3.J4.4 (J4.MX2+)
unnamed: MODULE1.J5 (RXC), T1.7
unnamed: MODULE1.J4 (TXC), T1.2
RST: MODULE1.RST, SW2.P$2 (2)
VDD_5V: C1.P$2 (2), CON11.7, CON11.8, MODULE1.5V
VDD_12V: CON11.9, CON11.10, CON11.11, MODULE3.SUP (SUPPLY)

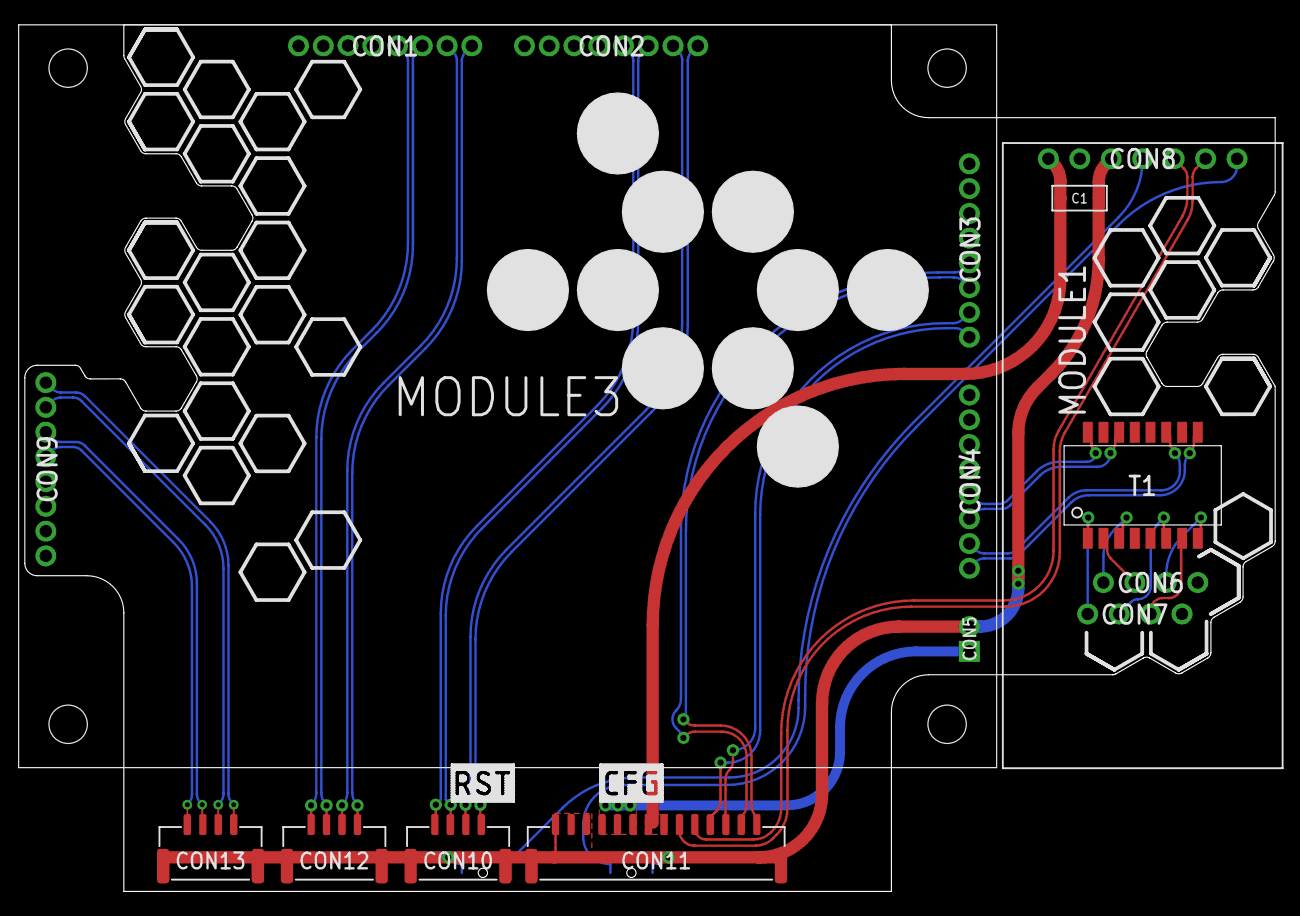
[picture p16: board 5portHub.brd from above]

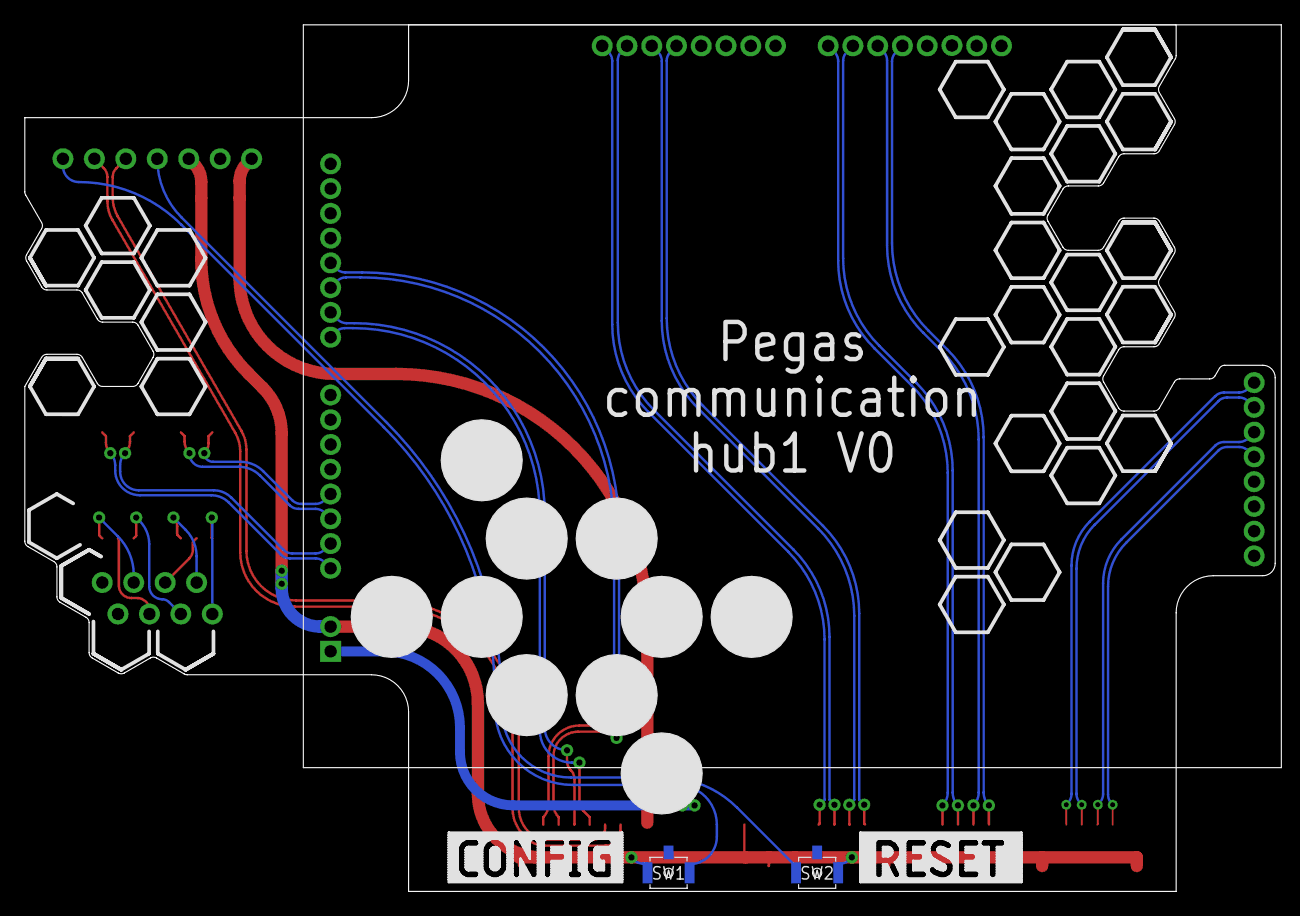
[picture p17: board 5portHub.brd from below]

Board: 2 copper layers, 101.0 x 70.0 mm, 12 parts (3 on the bottom side), 33 nets.

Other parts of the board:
U$1, U$2: AERODYNE

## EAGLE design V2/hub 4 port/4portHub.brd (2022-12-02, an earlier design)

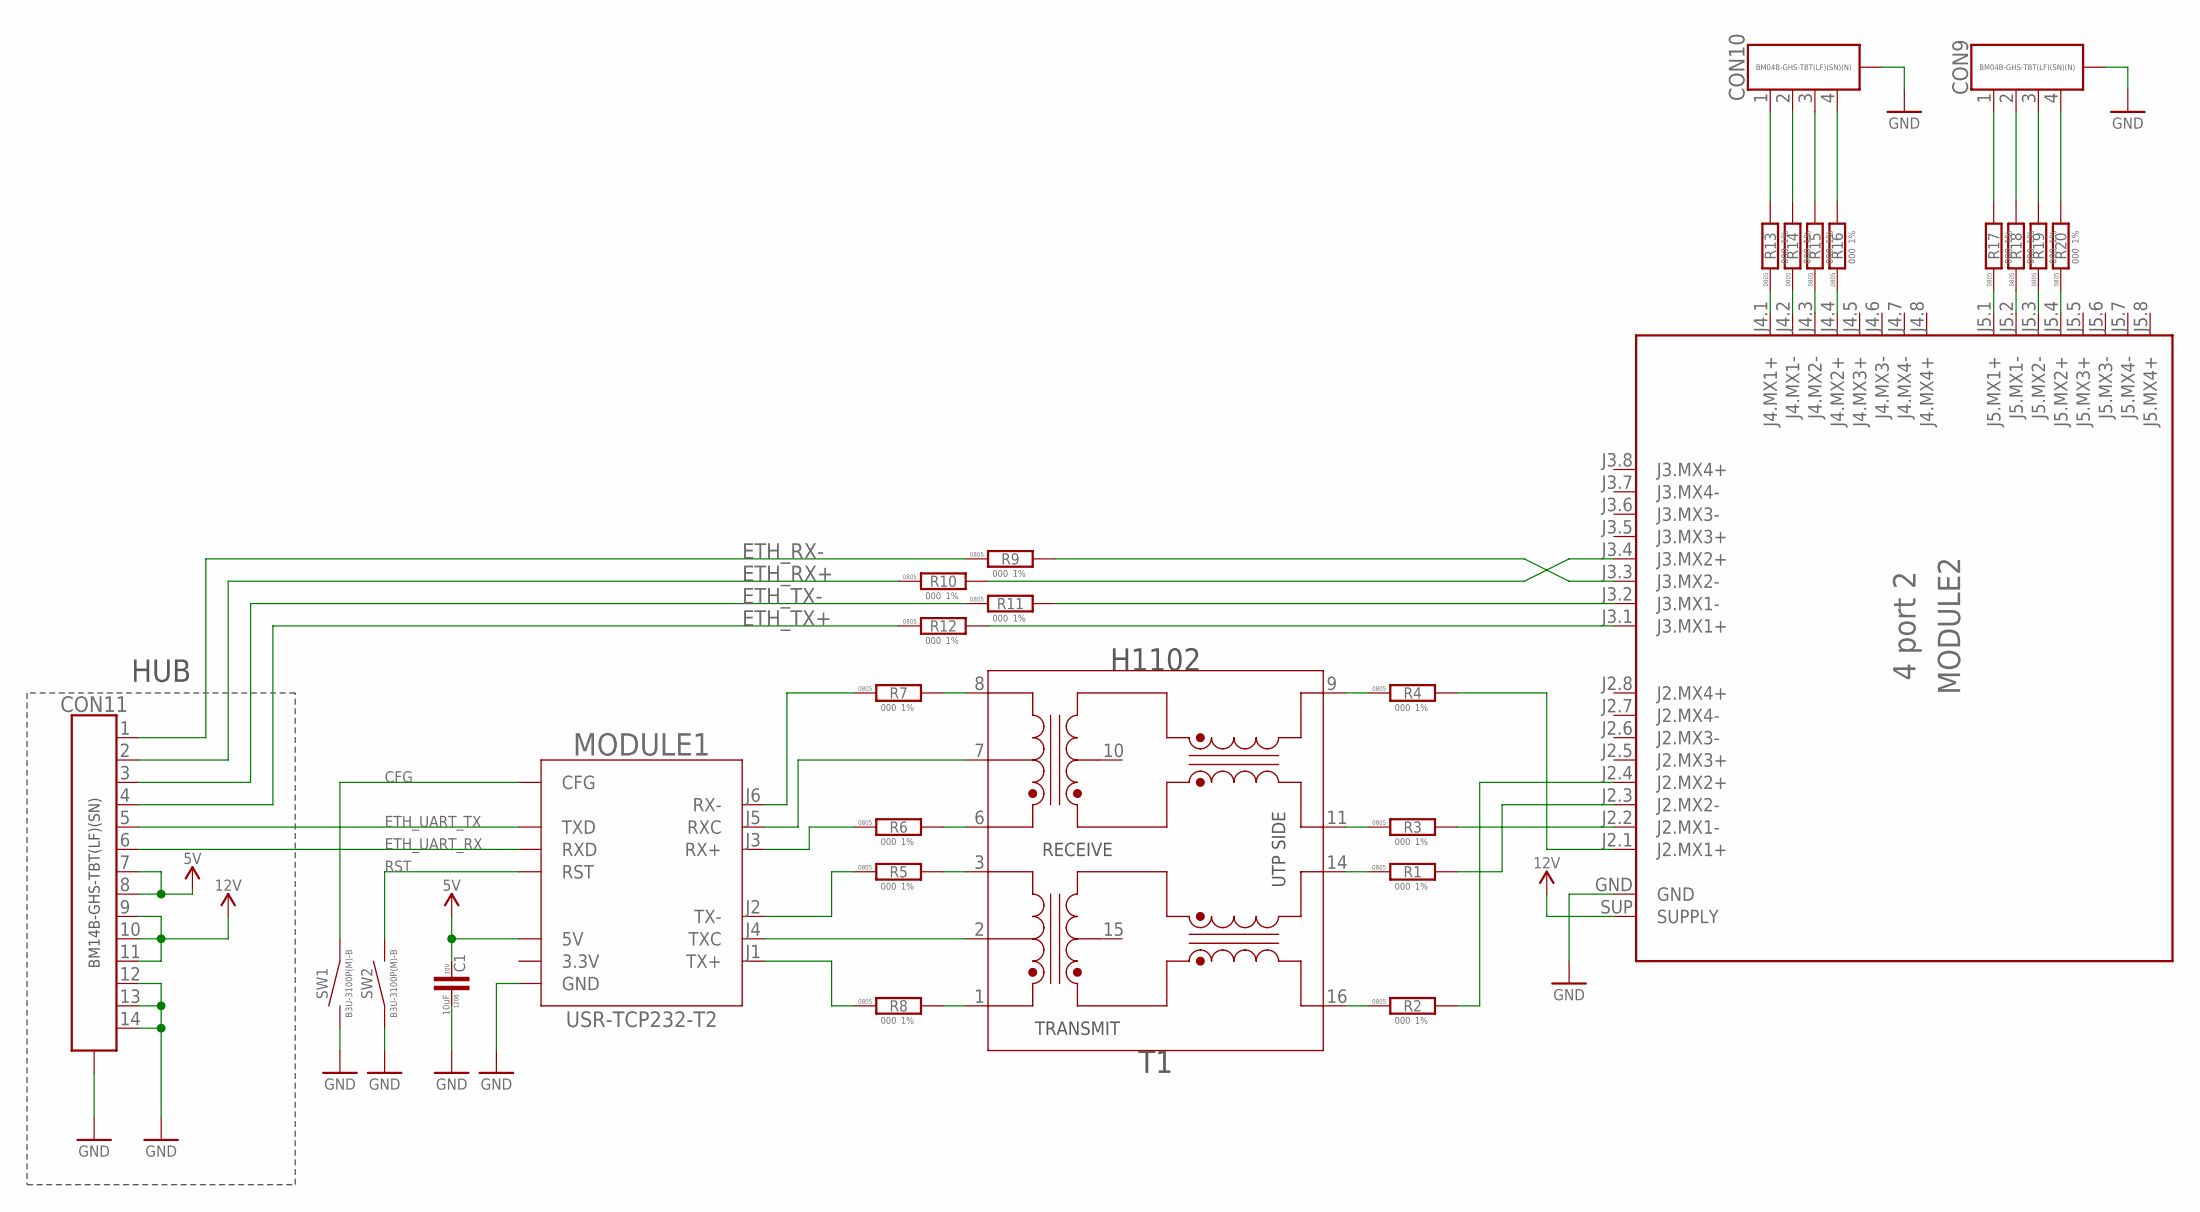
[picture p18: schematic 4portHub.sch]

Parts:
C1: 10uF; C1206; VOLTAGE 10V
CON9, CON10: CON-4P-TABS-JST-GH-TOP; BM04B-GHS-TB
CON11: CON-14P-TABS-JST-GH-TOP; BM14B-GHS-TBT
MODULE1: USR-TCP232-T2
MODULE2: ANDDEAR_4PORT2
R1, R2, R3, R4, R5, R6, R7, R8, R9, R10, R11, R12, R13, R14, R15, R16, R17, R18, R19, R20: 000; R0805
SW1, SW2: TACT_SWITCH-B3U-3100P(M)-B; B3U-3100P(M)-B
T1: H1102NL; H1102

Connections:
CFG: MODULE1.CFG, SW1.P$1 (1)
ETH_RX+: CON11.2, R10.1
ETH_RX-: CON11.1, R9.1
ETH_TX+: CON11.4, R12.1
ETH_TX-: CON11.3, R11.1
ETH_UART_RX: CON11.6, MODULE1.RXD
ETH_UART_TX: CON11.5, MODULE1.TXD
GND: C1.P$1 (1), CON9.M$0 (GND), CON9.M$1 (GND), CON10.M$0 (GND), CON10.M$1 (GND), CON11.12, CON11.13, CON11.14, CON11.M$0 (G1), CON11.M$1 (G1), MODULE1.GND, MODULE2.GND, SW1.P$2 (2), SW2.P$1 (1)
unnamed: R7.2, T1.8
unnamed: R6.2, T1.6
unnamed: R5.2, T1.3
unnamed: R8.2, T1.1
unnamed: R4.1, T1.9
unnamed: R3.1, T1.11
unnamed: R1.1, T1.14
unnamed: R2.1, T1.16
unnamed: MODULE2.J2.1 (J2.MX1+), R4.2
unnamed: MODULE2.J2.2 (J2.MX1-), R3.2
unnamed: MODULE2.J2.3 (J2.MX2-), R1.2
unnamed: MODULE2.J2.4 (J2.MX2+), R2.2
unnamed: MODULE1.J6 (RX-), R7.1
unnamed: MODULE1.J1 (TX+), R8.1
unnamed: MODULE1.J2 (TX-), R5.1
unnamed: MODULE1.J3 (RX+), R6.1
unnamed: MODULE2.J3.3 (J3.MX2-), R9.2
unnamed: MODULE2.J3.4 (J3.MX2+), R10.2
unnamed: MODULE2.J3.2 (J3.MX1-), R11.2
unnamed: MODULE2.J3.1 (J3.MX1+), R12.2
unnamed: CON9.1, R17.2
unnamed: CON9.2, R18.2
unnamed: CON9.3, R19.2
unnamed: CON9.4, R20.2
unnamed: CON10.1, R13.2
unnamed: CON10.2, R14.2
unnamed: CON10.3, R15.2
unnamed: CON10.4, R16.2
unnamed: MODULE2.J4.1 (J4.MX1+), R13.1
unnamed: MODULE2.J4.2 (J4.MX1-), R14.1
unnamed: MODULE2.J4.3 (J4.MX2-), R15.1
unnamed: MODULE2.J4.4 (J4.MX2+), R16.1
unnamed: MODULE2.J5.1 (J5.MX1+), R17.1
unnamed: MODULE2.J5.2 (J5.MX1-), R18.1
unnamed: MODULE2.J5.3 (J5.MX2-), R19.1
unnamed: MODULE2.J5.4 (J5.MX2+), R20.1
unnamed: MODULE1.J5 (RXC), T1.7
unnamed: MODULE1.J4 (TXC), T1.2
RST: MODULE1.RST, SW2.P$2 (2)
VDD_5V: C1.P$2 (2), CON11.7, CON11.8, MODULE1.5V
VDD_12V: CON11.9, CON11.10, CON11.11, MODULE2.SUP (SUPPLY)

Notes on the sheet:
HUB

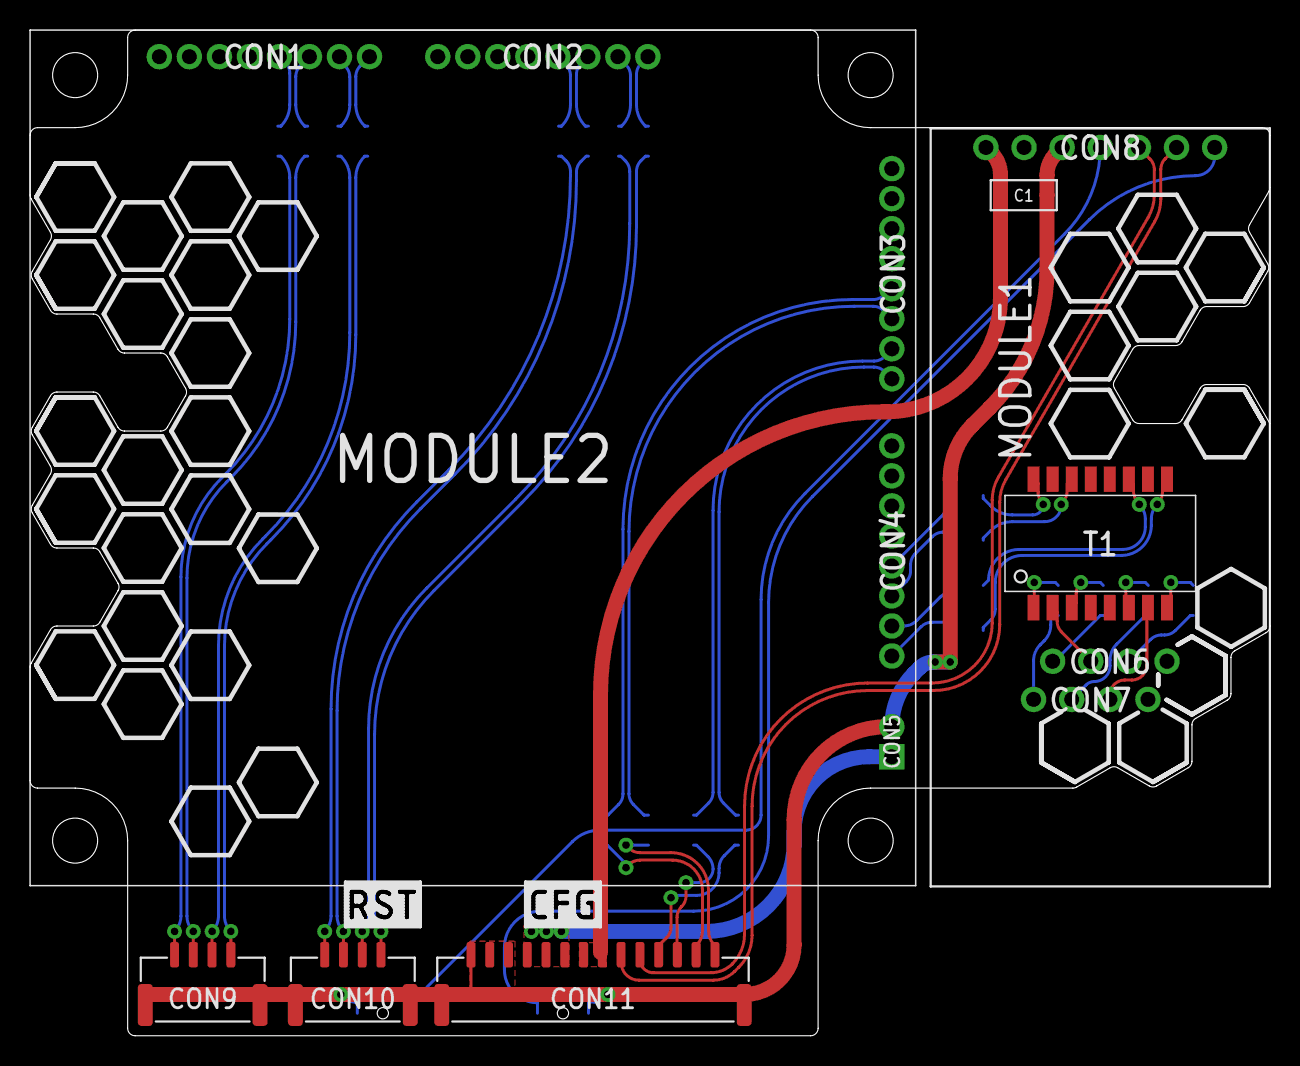
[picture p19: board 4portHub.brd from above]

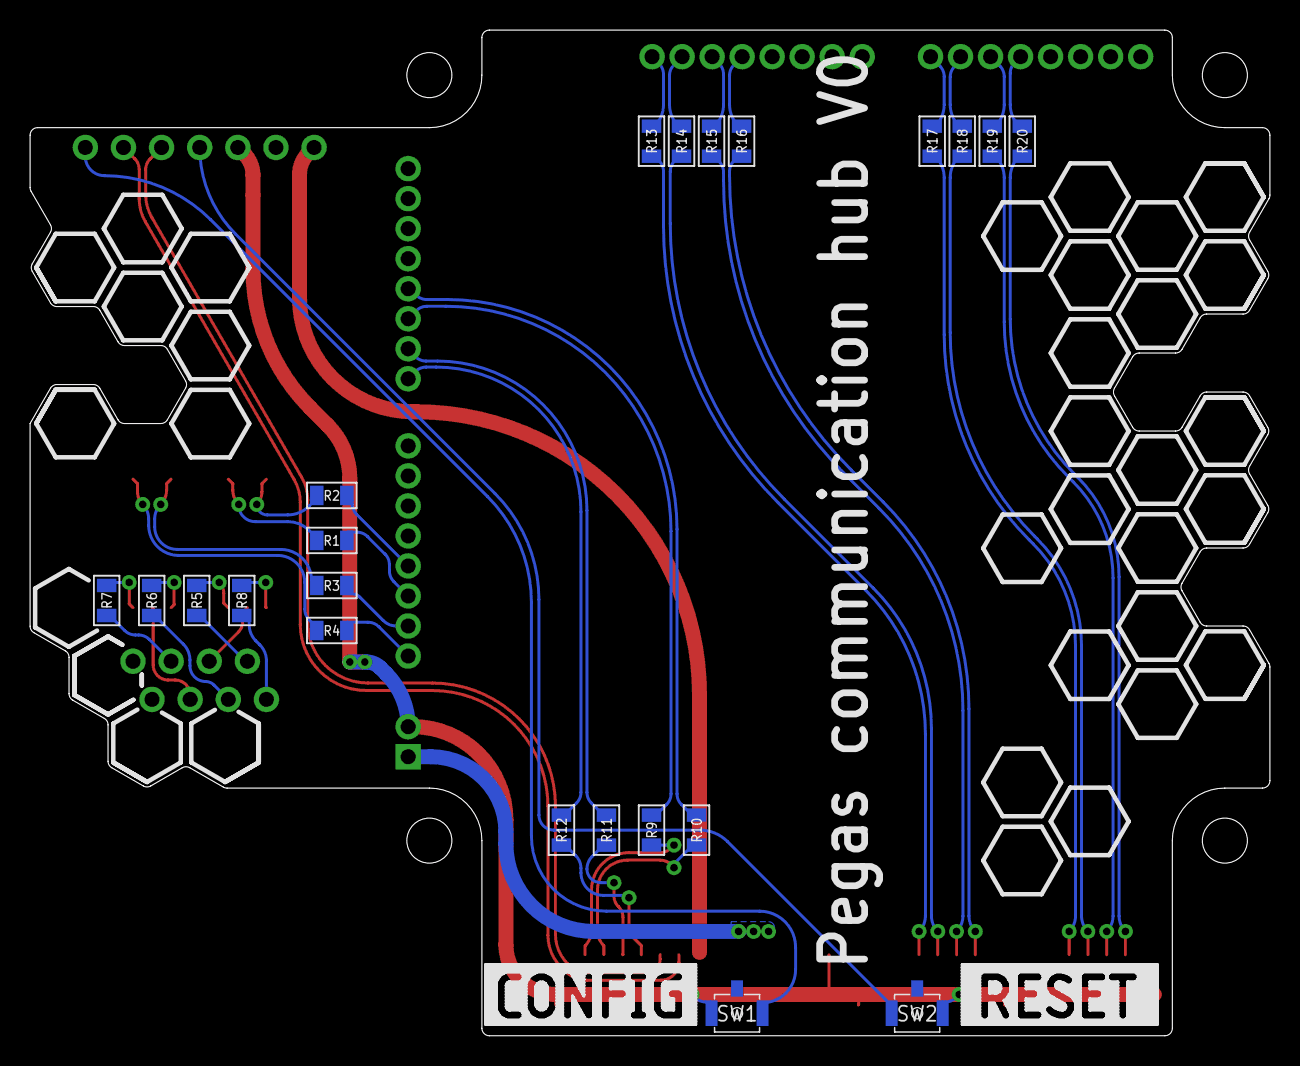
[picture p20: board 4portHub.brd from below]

Board: 2 copper layers, 82.6 x 67.0 mm, 29 parts (22 on the bottom side), 49 nets.

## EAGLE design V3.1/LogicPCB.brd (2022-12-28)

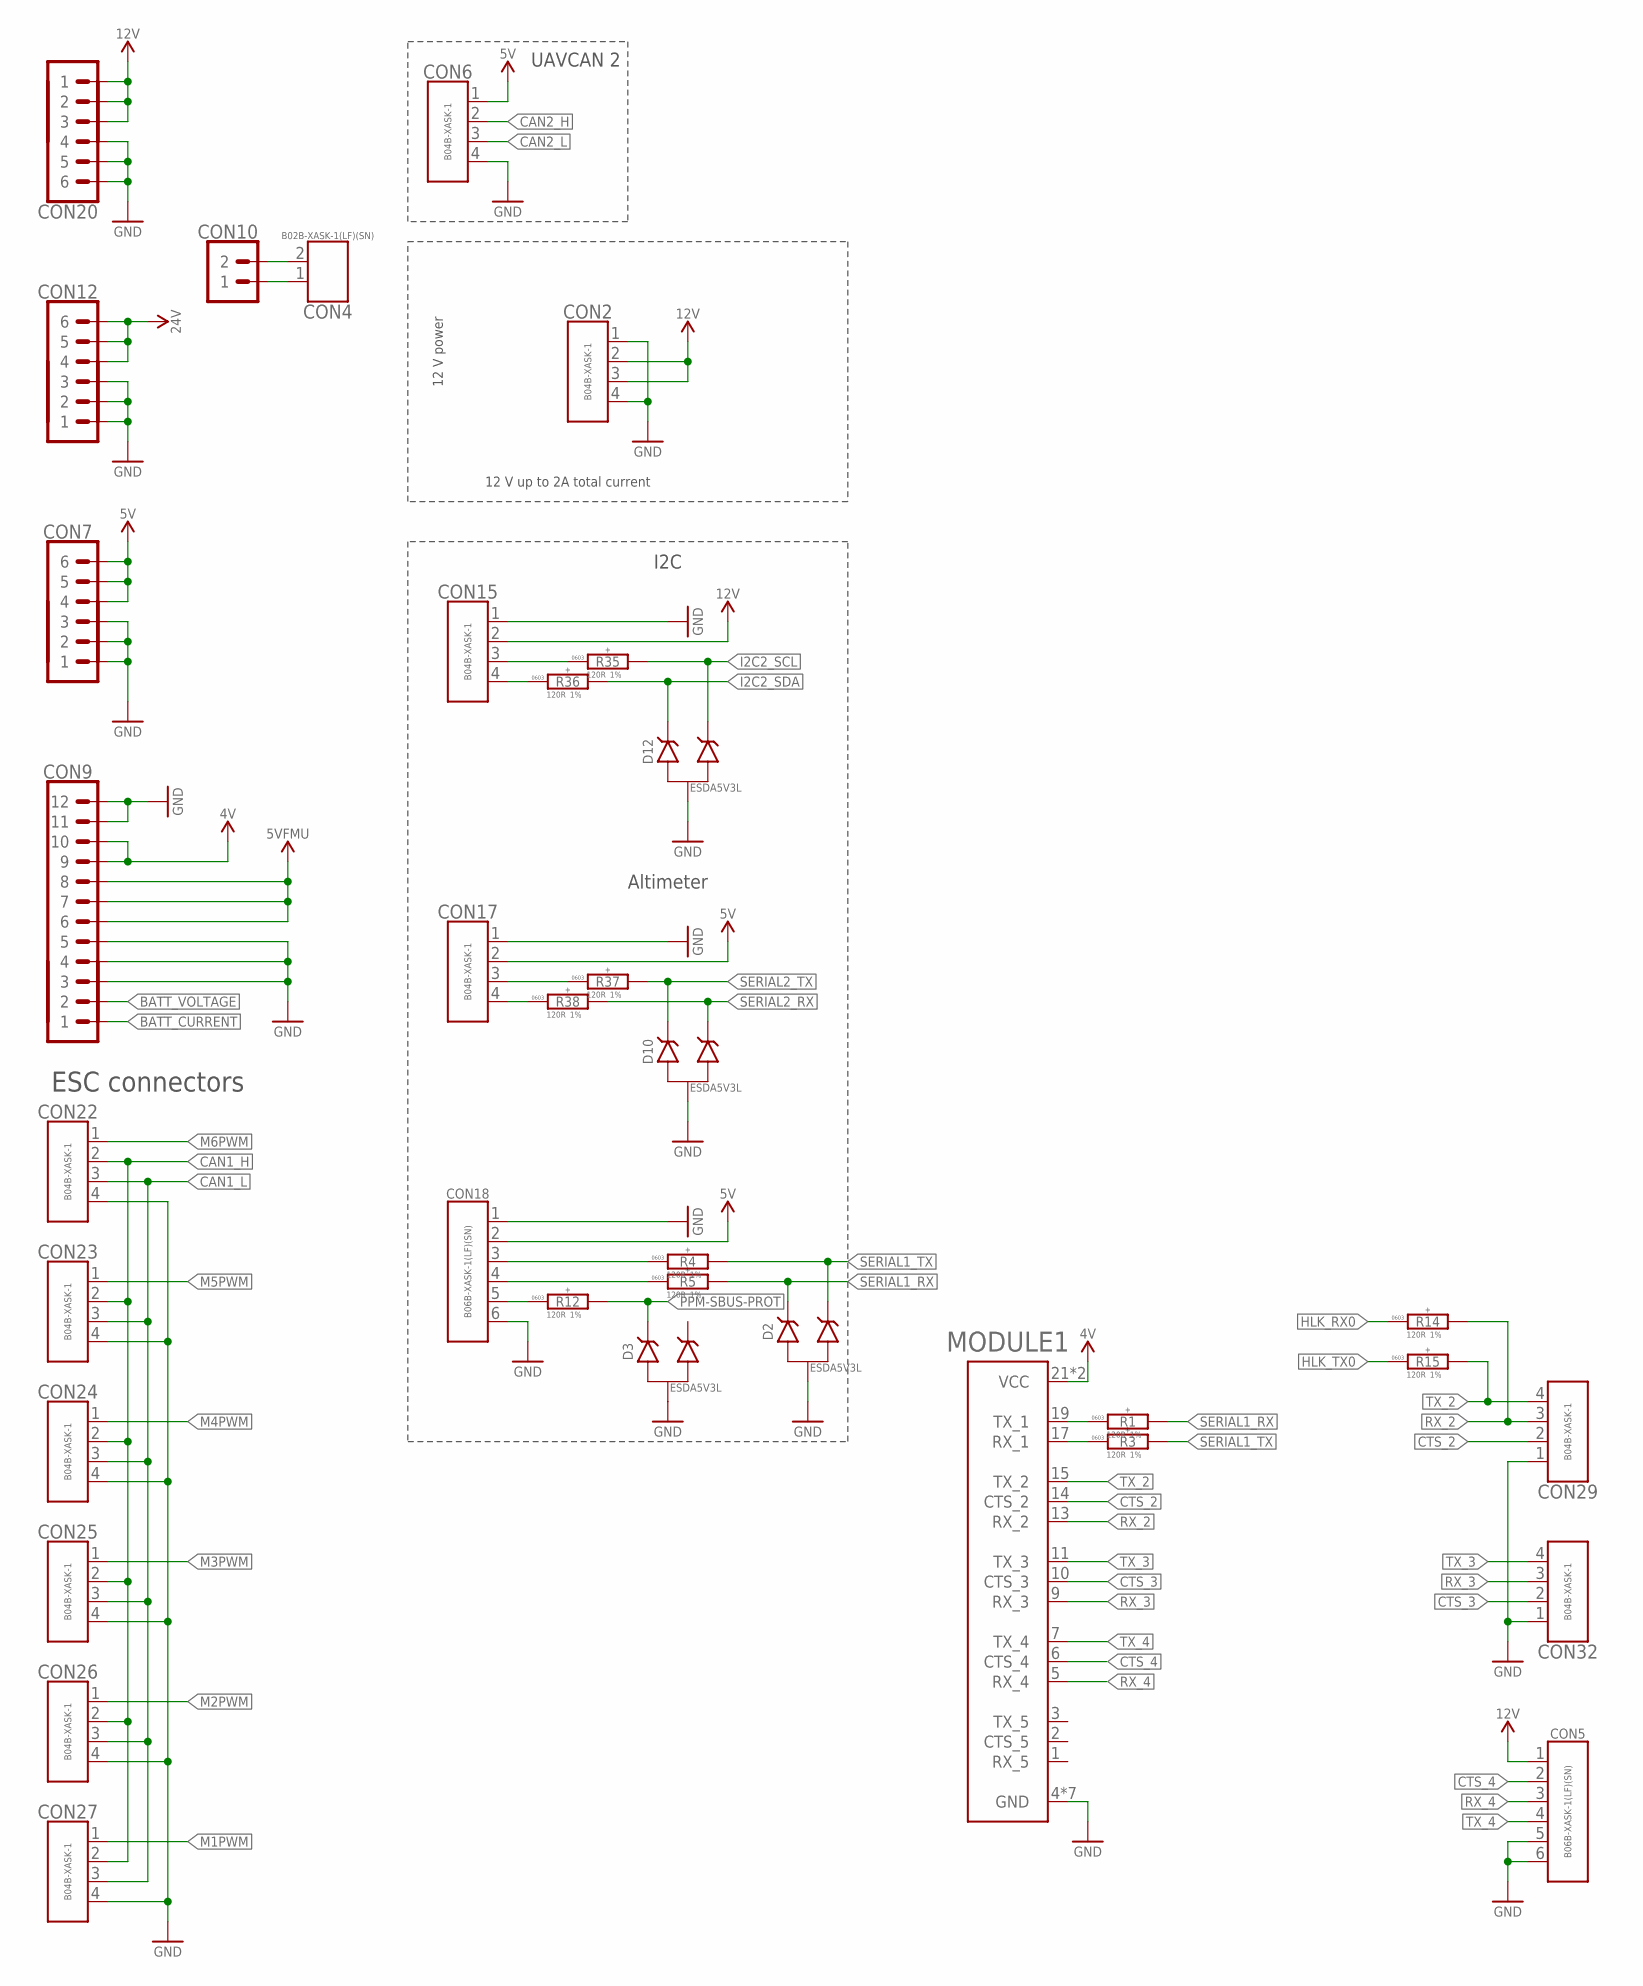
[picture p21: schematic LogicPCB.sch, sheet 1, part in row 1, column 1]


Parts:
BUZ1: BUZZER-ЕР-12MM; BUZZER_12MM
CON1: CUBE_ORANGE_; CUBE_ORANGE
CON2, CON6, CON11, CON15, CON17, CON22, CON23, CON24, CON25, CON26, CON27, CON28, CON29, CON30, CON32: CON-4P-JST-XA; B04B-XASK-1
CON4: CON-2P-JST-XA; B02B-XASK-1
CON5, CON18: CON-6P-JST-XA; B06B-XASK-1
CON7, CON12, CON20: PINHEAD_1X06-2.54; 1X06-PTH-2.54
CON9: PINHEAD_1X12-2.54; 1X12-PTH-2.54
CON10: PINHEAD_1X02-2.54; 1X02-PTH-2.54
CON14: PINHEAD_1X04-2.54; 1X04-PTH-2.54
CON19: USB-TYPE-C-VERT-PROD; 2047110001-PROD; LCSC# C381139
D1: SS34; DO-214AC(SMA)
D2, D3, D10, D12: ESDA5V3L; SOT23B-3
LED4: LED-0603; LED0603; LCSC# C2286
MODULE1: MODEM_CARRIER
Q1: IRLML0030; SOT23
R1, R2, R3, R4, R5, R12, R14, R15, R20, R35, R36, R37, R38: 120R; R0603; LCSC# C22787
R16: 51K; R0603; LCSC# C23196
R18: 1K; R0603; LCSC# C21190
R22: 200R; R1206; LCSC# C25361
R23: DNM; R1206
SJ2: SOLDER_JOINT-SJ1; RES_0

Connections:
5VFMU: CON1.61 (VDD_5V), CON1.63 (VDD_5V), CON9.6, CON9.7, CON9.8, D1.C, R18.1
!FMU_LED_AMBER: CON1.2 (!FMU_LED_AMBER), LED4.C
ALARM: CON1.24 (ALARM), R20.2
BATT_CURRENT: CON1.49 (BATT_CURRENT_SENS_PROT), CON9.1
BATT_VOLTAGE: CON1.47 (BATT_VOLTAGE_SENS_PROT), CON9.2
CAN1_H: CON1.79 (CAN1_H), CON22.2, CON23.2, CON24.2, CON25.2, CON26.2, CON27.2, CON28.2, R2.1
CAN1_L: CON1.77 (CAN1_L), CON22.3, CON23.3, CON24.3, CON25.3, CON26.3, CON27.3, CON28.3, SJ2.2
CAN2_H: CON1.41 (CAN2_H), CON6.2
CAN2_L: CON1.39 (CAN2_L), CON6.3
CTS_2: CON29.2, MODULE1.14 (CTS_2)
CTS_3: CON32.2, MODULE1.10 (CTS_3)
CTS_4: CON5.2, MODULE1.6 (CTS_4)
GND: CON1.13 (GND), CON1.15 (GND), CON1.55 (!VDD_BRICK_VALID\), CON2.1, CON2.4, CON5.5, CON5.6, CON6.4, CON7.1, CON7.2, CON7.3, CON9.3, CON9.4, CON9.5, CON9.11, CON9.12, CON11.1, CON12.1, CON12.2, CON12.3, CON14.1, CON15.1, CON17.1, CON18.1, CON18.6, CON19.A1 (GND), CON19.A12 (GND), CON19.B1 (GND), CON19.B12 (GND), CON19.G1 (GND), CON19.G2 (GND), CON19.G4 (GND), CON19.G5 (GND), CON19.G7 (GND), CON19.G8 (GND), CON19.G9 (GND), CON19.G10 (GND), CON19.P$1 (GND), CON19.P$2 (GND), CON20.4, CON20.5, CON20.6, CON22.4, CON23.4, CON24.4, CON25.4, CON26.4, CON27.4, CON28.4, CON29.1, CON30.1, CON32.1, D2.3 (A), D3.3 (A), D10.3 (A), D12.3 (A), MODULE1.4 (GND), MODULE1.8 (GND), MODULE1.12 (GND), MODULE1.16 (GND), MODULE1.20 (GND), MODULE1.22 (GND), MODULE1.24 (GND), Q1.2 (S), R16.1; also elsewhere on the board
HLK_RX0: R14.1; also elsewhere on the board
HLK_TX0: R15.1; also elsewhere on the board
I2C2_SCL: CON1.6 (I2C2_SCL), D12.2 (C1), R35.2
I2C2_SDA: CON1.4 (I2C2_SDA), D12.1 (C), R36.2
M1PWM: CON1.50 (FMU-CH1-PROT), CON27.1
M2PWM: CON1.52 (FMU-CH2-PROT), CON26.1
M3PWM: CON1.54 (FMU-CH3-PROT), CON25.1
M4PWM: CON1.56 (FMU-CH4-PROT), CON24.1
M5PWM: CON1.58 (FMU-CH5-PROT), CON23.1
M6PWM: CON1.60 (FMU-CH6-PROT), CON22.1
unnamed: LED4.A, R18.2
unnamed: CON4.1, CON10.1
unnamed: BUZ1.2 (-), Q1.3 (D)
unnamed: MODULE1.19 (TX_1), R1.1
unnamed: Q1.1 (G), R16.2, R20.1
unnamed: MODULE1.17 (RX_1), R3.1
unnamed: CON4.2, CON10.2
unnamed: R2.2, SJ2.1
unnamed: CON18.3, R4.1
unnamed: CON18.4, R5.1
unnamed: BUZ1.1 (+), R22.P$1 (1), R23.P$1 (1)
unnamed: CON18.5, R12.1
unnamed: CON15.3, R35.1
unnamed: CON15.4, R36.1
unnamed: CON17.3, R37.1
unnamed: CON17.4, R38.1
OTG_DM1: CON1.33 (OTG_DM1), CON14.4, CON19.A7 (D-), CON19.B7 (D-)
OTG_DP1: CON1.31 (OTG_DP1), CON14.3, CON19.A6 (D+), CON19.B6 (D+)
PPM-SBUS-PROT: CON1.62 (PPM-SBUS-PROT), D3.1 (C), R12.2
RX_2: CON29.3, MODULE1.13 (RX_2), R14.2
RX_3: CON32.3, MODULE1.9 (RX_3)
RX_4: CON5.3, MODULE1.5 (RX_4)
SERIAL1_RX: CON1.38 (SERIAL1_RX), D2.1 (C), R1.2, R5.2; also elsewhere on the board
SERIAL1_TX: CON1.40 (SERIAL1_TX), D2.2 (C1), R3.2, R4.2; also elsewhere on the board
SERIAL2_RX: CON1.34 (SERIAL2_RX), D10.2 (C1), R38.2
SERIAL2_TX: CON1.36 (SERIAL2_TX), D10.1 (C), R37.2
SERIAL3_RX: CON1.20 (SERIAL3_RX); also elsewhere on the board
SERIAL3_TX: CON1.22 (SERIAL3_TX); also elsewhere on the board
SERIAL4_RX: CON1.16 (SERIAL4_RX), CON11.4
SERIAL4_TX: CON1.18 (SERIAL4_TX), CON11.3
SERIAL5_RX: CON1.12 (SERIAL5_RX), CON30.4
SERIAL5_TX: CON1.14 (SERIAL5_TX), CON30.3
TX_2: CON29.4, MODULE1.15 (TX_2), R15.2
TX_3: CON32.4, MODULE1.11 (TX_3)
TX_4: CON5.4, MODULE1.7 (TX_4)
VBUS: CON1.29 (VBUS), CON14.2, CON19.A4 (VBUS), CON19.B4 (VBUS), D1.A
VDD_4V: CON9.9, CON9.10, MODULE1.21 (VCC), MODULE1.23 (VCC)
VDD_5V: CON6.1, CON7.4, CON7.5, CON7.6, CON11.2, CON17.2, CON18.2, CON28.1, CON30.2, R23.P$2 (2)
VDD_12V: CON2.2, CON2.3, CON5.1, CON15.2, CON20.1, CON20.2, CON20.3, R22.P$2 (2); also elsewhere on the board
VDD_24V: CON12.4, CON12.5, CON12.6; also elsewhere on the board

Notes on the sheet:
12 V up to 2A total current
12 V power
GNSS UAVCAN
UAVCAN
UAVCAN 2
CAN buses are terminated inside Cube orange
CAN2 -> Smart batteries UAVCAN network CAN1 -> GNSS module communication Serial1 -> TELEMETRY Serial2 -> BACKUP Serial3 -> PAYLOAD Serial4 -> BEACON Serial5 -> BACKUP UART
USB
VDD_BRICK_VALID should be pulled low to make PX4 measure battery voltage and current
Buzzer https://www.chipdip.ru/product/hcm1212a or probably https://www.chipdip.ru/product/hcm1203x
ESC connectors
Altimeter
I2C

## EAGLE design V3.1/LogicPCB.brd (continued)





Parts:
C4: 10u; C1206; VOLTAGE 25V; LCSC# C77090
C8: 47u; C1206; VOLTAGE 25V; LCSC# C403725
C56: 10n; C0603; VOLTAGE 50V
CON3: RJ45-NO_SHIELD-5556416-1; 5556416-1
CON8, CON13, CON16: CON-6P-JST-XA; B06B-XASK-1
CON21: CON-4P-JST-XA; B04B-XASK-1
D11: SS34; DO-214AC(SMA)
IC5: AOZ1280; SOT23-6
L1: 3.3uH; IHLP-2020BZ-01
LED1, LED2, LED3, LED5: LED-0603; LED0603; LCSC# C2286
M1: 05G_ETHERNET_SWITCH; 05G_ETH_SWITCH
MODULE2: HLK-7688A
PAD1, PAD2: PAD-HEX-2MM; HEX-2MM
R6, R7: 120R; R0603; LCSC# C22787
R8, R9, R10, R11: 1K; R0603; LCSC# C21190
R30, R32: 51K; R0603; LCSC# C23196
R31: 16K; R0603; LCSC# C25804
T1, T2, T3, T4: H1102NL; H1102

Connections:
DBG_ETH_RX+: CON3.1, M1.J4.1 (TX+), T4.16
DBG_ETH_RX-: CON3.2, M1.J4.2 (TX-), T4.14
DBG_ETH_TX+: CON3.3, M1.J4.3 (RX+), T4.11
DBG_ETH_TX-: CON3.6, M1.J4.6 (RX-), T4.9
ETH1_RX+: CON21.2, M1.J1.3 (RX+), T2.11
ETH1_RX-: CON21.1, M1.J1.6 (RX-), T2.9
ETH1_TX+: CON21.4, M1.J1.1 (TX+), T2.16
ETH1_TX-: CON21.3, M1.J1.2 (TX-), T2.14
ETH3_RX+: CON13.4, M1.J3.3 (RX+), T1.11
ETH3_RX-: CON13.5, M1.J3.6 (RX-), T1.9
ETH3_TX+: CON13.2, M1.J3.1 (TX+), T1.16
ETH3_TX-: CON13.3, M1.J3.2 (TX-), T1.14
ETH5_RX+: CON8.3, M1.J5.3 (RX+), T3.11
ETH5_RX-: CON8.4, M1.J5.6 (RX-), T3.9
ETH5_TX+: CON8.1, M1.J5.1 (TX+), T3.16
ETH5_TX-: CON8.2, M1.J5.2 (TX-), T3.14
GND: C4.P$1 (1), C8.P$2 (2), CON8.6, CON13.6, CON16.6, D11.A, IC5.2 (GND), LED1.C, LED2.C, LED3.C, LED5.C, M1.GND, MODULE2.1 (GND), MODULE2.4 (GND), MODULE2.21 (GND), MODULE2.23 (GND), MODULE2.56 (GND), MODULE2.P$1 (GND), MODULE2.P$2 (GND), MODULE2.P$3 (GND), R31.2; also elsewhere on the board
HLK_RX0: CON16.2, MODULE2.32 (UART_RXD0); also elsewhere on the board
HLK_RX1: MODULE2.16 (UART_RXD1), R6.1
HLK_TX0: CON16.1, MODULE2.31 (UART_TXD0); also elsewhere on the board
HLK_TX1: MODULE2.15 (UART_TXD1), R7.1
LINK2: MODULE2.11 (EPHY_LED2), R9.2
LINK4: MODULE2.9 (EPHY_LED4), R8.2
unnamed: LED1.A, R8.1
unnamed: LED2.A, R9.1
unnamed: LED3.A, R10.1
unnamed: LED5.A, R11.1
unnamed: MODULE2.12 (EPHY_LED1), R10.2
unnamed: MODULE2.13 (EPHY_LED0), R11.2
unnamed: C56.2, IC5.1 (BST)
unnamed: IC5.3 (FB), R30.1, R31.1
unnamed: IC5.4 (EN), R32.1
P0_RX+: MODULE2.34 (MDI_RP_P0), T2.6
P0_RX-: MODULE2.35 (MDI_RN_P0), T2.8
P0_TX+: MODULE2.36 (MDI_TP_P0), T2.1
P0_TX-: MODULE2.37 (MDI_TN_P0), T2.3
P1_RX+: MODULE2.40 (MDI_RP_P1), T1.6
P1_RX-: MODULE2.41 (MDI_RN_P1), T1.8
P1_TX+: MODULE2.38 (MDI_TP_P1), T1.1
P1_TX-: MODULE2.39 (MDI_TN_P1), T1.3
P2_RX+: MODULE2.42 (MDI_RP_P2), T4.6
P2_RX-: MODULE2.43 (MDI_RN_P2), T4.8
P2_TX+: MODULE2.44 (MDI_TP_P2), T4.1
P2_TX-: MODULE2.45 (MDI_TN_P2), T4.3
P4_RX+: MODULE2.50 (MDI_RP_P4), T3.6
P4_RX-: MODULE2.51 (MDI_RN_P4), T3.8
P4_TX+: MODULE2.52 (MDI_TP_P4), T3.1
P4_TX-: MODULE2.53 (MDI_TN_P4), T3.3
SERIAL1_RX: R7.2; also elsewhere on the board
SERIAL1_TX: R6.2; also elsewhere on the board
SERIAL3_RX: CON16.4; also elsewhere on the board
SERIAL3_TX: CON16.3; also elsewhere on the board
SW: C56.1, D11.C, IC5.6 (SW), L1.P$1 (1)
USB_DM: MODULE2.55 (USB_DM), PAD2.1
USB_DP: MODULE2.54 (USB_DP), PAD1.1
VDD_3V3: C8.P$1 (1), L1.P$2 (2), MODULE2.2 (3.3V), MODULE2.3 (3.3V), R30.2
VDD_12V: C4.P$2 (2), CON13.1, IC5.5 (VIN), M1.SUP, R32.2; also elsewhere on the board
VDD_24V: CON8.5, CON16.5; also elsewhere on the board

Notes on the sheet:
Vout = 3.35V
PAYLOAD



Board: 2 copper layers, 171.9 x 151.6 mm, 85 parts (7 on the bottom side), 112 nets.

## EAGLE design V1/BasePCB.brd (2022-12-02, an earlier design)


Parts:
BAT1PAD1, BAT1PAD2, BAT2PAD1, BAT2PAD2, BAT3PAD1, BAT3PAD2: PAD_PAIR-4X10; 4X10_PAIR
C1: 0.1uF; C0603; VOLTAGE 50V; LCSC# C14663
C3, C4: DNP; C0603
CON1: CON-80P-DF17(1.0H)-80DP-0.5V; DF17(1.0H)-80DP-0.5V
CON2: CON-3P-TABS-JST-GH-SIDE; SM03B-GHS-TB
CON3, CON4, CON5: CON-4P-TABS-JST-GH-SIDE; SM04B-GHS-TB
CON6, CON7, CON8, CON9, CON10, CON11, CON12, CON13, CON17, CON20, CON21: CON-4P-TABS-JST-GH-TOP; BM04B-GHS-TB
CON14, CON15: PINHEAD_1X04-2.54; 1X04-PTH-2.54
CON16: CON-6P-TABS-JST-GH-TOP; BM06B-GHS-TBT
CON18: CON-14P-TABS-JST-GH-TOP; BM14B-GHS-TBT
CON19: USB-TYPE-C-VERT-PROD; 2047110001-PROD; LCSC# C381139
D1: MBR0520L-SOD123; SOD123
IC1: INA169; SOT23-5
J1: CONNECTION-SMD-BIG; CONNECTION_BIG
LED4: LED-0603; LED0603; LCSC# C2286
M1, M2, M3, M4, M5, M6: PAD_PAIR-4X10; 4X10_PAIR
PAD1, PAD2, PAD5, PAD6, PAD7, PAD10: PAD-10X4; 10X4
PAD3, PAD4, PAD25, PAD26, PAD27: PAD-S_2X2; 2х2
PAD28, PAD29, PAD30, PAD31, PAD32, PAD33: PAD_PAIR-2X6; 2X6_PAIR
R1, R2: 120R; R0603; LCSC# C22787
R3, R14, R15: 82K; R0603; LCSC# C23254
R4: 200 µOhms; R3920-KELVIN
R13: 10K2; R0603; LCSC# C22772
R18: 1K; R0603; LCSC# C21190
SJ2: SOLDER_JOINT-SJ1; RES_0

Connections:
!EXTERN_CS: CON1.5
!FMU_LED_AMBER: CON1.2, LED4.C
!IO-LED_SAFET_PROT: CON1.28
!VBUS_VALID: CON1.59
!VDD_5V_HIPOWER_OC: CON1.45
!VDD_5V_PERIPH_EN: CON1.27
!VDD_5V_PERIPH_OC: CON1.43
!VDD_BACKUP_VALID: CON1.57
ALARM: CON1.24
AUX_BATT_CURRENT_SENS: CON1.25
AUX_BATT_VOLTAGE_SENS: CON1.23
BAT1_MID: BAT1PAD2.1, PAD7.P$1
BAT2_MID: BAT2PAD2.1, PAD2.P$1
BAT3_MID: BAT3PAD2.1, PAD6.P$1
BATT_CURRENT_SENS_PROT: C3.2, CON1.49, IC1.1 (OUT), R3.2
BATT_VOLTAGE_SENS_PROT: C4.2, CON1.47, R13.2, R15.1
CAN1_H: CON1.79, CON20.2, R2.1
CAN1_L: CON1.77, CON20.3, SJ2.2
CAN2_H: CON1.41, CON6.2, CON7.2, CON8.2, CON9.2, CON10.2, CON11.2, CON12.2, CON21.2, R1.1
CAN2_L: CON1.39, CON6.3, CON7.3, CON8.3, CON9.3, CON10.3, CON11.3, CON12.3, CON21.3, R1.2
CAN3_H: CON1.10
CAN3_L: CON1.8
ETH_RX+: CON5.2, CON18.2
ETH_RX-: CON5.1, CON18.1
ETH_TX+: CON5.4, CON18.4
ETH_TX-: CON5.3, CON18.3
EXTERN_DRDY: CON1.11
FMU-!RESET: CON1.7, PAD27.P$1
FMU-CH1-PROT/MOTOR1: CON1.50, PAD28.2
FMU-CH2-PROT/MOTOR2: CON1.52, PAD29.2
FMU-CH3-PROT/MOTOR3: CON1.54, PAD30.2
FMU-CH4-PROT/MOTOR4: CON1.56, PAD31.2
FMU-CH5-PROT/MOTOR5: CON1.58, PAD32.2
FMU-CH6-PROT/MOTOR6: CON1.60, PAD33.2
FMU-SWCLK: CON1.3, PAD25.P$1
FMU-SWDIO: CON1.1, PAD26.P$1
GND: C1.1, C3.1, C4.1, CON1.13, CON1.15, CON1.55, CON2.1, CON2.M$0 (GND), CON2.M$1 (GND), CON3.1, CON3.4, CON3.M$0 (GND), CON3.M$1 (GND), CON4.1, CON4.M$0 (GND), CON4.M$1 (GND), CON5.M$0 (GND), CON5.M$1 (GND), CON6.4, CON6.M$0 (GND), CON6.M$1 (GND), CON7.4, CON7.M$0 (GND), CON7.M$1 (GND), CON8.4, CON8.M$0 (GND), CON8.M$1 (GND), CON9.4, CON9.M$0 (GND), CON9.M$1 (GND), CON10.4, CON10.M$0 (GND), CON10.M$1 (GND), CON11.4, CON11.M$0 (GND), CON11.M$1 (GND), CON12.4, CON12.M$0 (GND), CON12.M$1 (GND), CON13.1, CON13.M$0 (GND), CON13.M$1 (GND), CON14.1, CON15.1, CON16.1, CON16.M$0 (G1), CON16.M$1 (G1), CON17.1, CON17.M$0 (GND), CON17.M$1 (GND), CON18.12, CON18.13, CON18.14, CON18.M$0 (G1), CON18.M$1 (G1), CON19.A1 (GND), CON19.A12 (GND), CON19.B1 (GND), CON19.B12 (GND), CON19.G1 (GND), CON19.G2 (GND), CON19.G4 (GND), CON19.G5 (GND), CON19.G7 (GND), CON19.G8 (GND), CON19.G9 (GND), CON19.G10 (GND), CON19.P$1 (GND), CON19.P$2 (GND), CON20.4, CON20.M$0 (GND), CON20.M$1 (GND), CON21.4, CON21.M$0 (GND), CON21.M$1 (GND), IC1.2 (GND), J1.1, PAD4.P$1, PAD28.1, PAD29.1, PAD30.1, PAD31.1, PAD32.1, PAD33.1, R3.1, R13.1; also elsewhere on the board
I2C1_SCL: CON1.37
I2C1_SDA: CON1.35
I2C2_SCL: CON1.6, CON15.3
I2C2_SDA: CON1.4, CON15.4
IO-!RESET: CON1.75
IO-CH1-PROT: CON1.80, CON16.2
IO-CH2-PROT: CON1.78, CON16.3
IO-CH3-PROT: CON1.76, CON16.4
IO-CH4-PROT: CON1.74, CON16.5
IO-CH5-PROT: CON1.72, CON16.6
IO-CH6-PROT: CON1.70
IO-CH7-PROT/24V_EN: CON1.68; also elsewhere on the board
IO-CH8-PROT/12V_EN: CON1.66; also elsewhere on the board
IO-SWCLK: CON1.71
IO-SWDIO: CON1.69
IO_USART1_RX_SPECTRUM_DSM: CON1.48
IO_USART1_TX: CON1.46
IO_VDD_3V3: CON1.26
IO_VDD_5V5: CON1.65
unnamed: LED4.A, R18.2
unnamed: BAT1PAD1.2, PAD1.P$1
unnamed: BAT2PAD1.2, PAD5.P$1
unnamed: BAT3PAD1.2, PAD10.P$1
unnamed: R2.2, SJ2.1
unnamed: IC1.4 (VIN-), R4.S2
unnamed: IC1.3 (VIN+), R4.S1
unnamed: R14.1, R15.2
OTG_DM1: CON1.33, CON14.4, CON19.A7 (D-), CON19.B7 (D-)
OTG_DP1: CON1.31, CON14.3, CON19.A6 (D+), CON19.B6 (D+)
PGND: BAT1PAD2.2, BAT2PAD2.2, BAT3PAD2.2, J1.2, M1.2, M2.2, M3.2, M4.2, M5.2, M6.2
PPM-SBUS-PROT: CON1.62, CON2.3
PRESSURE_SENS_IN: CON1.21
S.BUS_OUT: CON1.64
SAFETY: CON1.17
SERIAL1_CTS: CON1.44
SERIAL1_RTS: CON1.42
SERIAL1_RX: CON1.38, CON18.6
SERIAL1_TX: CON1.40, CON18.5
SERIAL2_CTS: CON1.32
SERIAL2_RTS: CON1.30
SERIAL2_RX: CON1.34, CON18.8
SERIAL2_TX: CON1.36, CON18.7
SERIAL3_RX: CON1.20, CON4.4
SERIAL3_TX: CON1.22, CON4.3
SERIAL4_RX: CON1.16, CON13.4
SERIAL4_TX: CON1.18, CON13.3
SERIAL5_RX: CON1.12, CON17.4
SERIAL5_TX: CON1.14, CON17.3
SPI_EXT_MISO: CON1.67
SPI_EXT_MOSI: CON1.51
SPI_EXT_SCK: CON1.73
VBAT: BAT1PAD1.1, BAT2PAD1.1, BAT3PAD1.1, R4.1, R4.11 (1), R14.2
VBUS: CON1.29, CON14.2, CON19.A4 (VBUS), CON19.B4 (VBUS), D1.A
VDC: M1.1, M2.1, M3.1, M4.1, M5.1, M6.1, R4.2, R4.22 (2); also elsewhere on the board
VDD_3V3_SPEKTRUM_EN: CON1.19
VDD_5V: C1.2, CON1.61, CON1.63, CON2.2, CON4.2, CON6.1, CON7.1, CON8.1, CON9.1, CON10.1, CON11.1, CON12.1, CON13.2, CON15.2, CON17.2, CON20.1, CON21.1, D1.C, IC1.5 (V+), PAD3.P$1, R18.1; also elsewhere on the board
VDD_12V: CON3.2, CON3.3; also elsewhere on the board
VDD_24V: CON18.9, CON18.10, CON18.11; also elsewhere on the board
VDD_SERVO: CON1.53
VDD_SERVO_IN: CON1.9

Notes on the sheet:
SBUS
12 V up to 2A total current
12 V power
UART (telem)
Ethernet
Radiointerfaces
GNSS UAVCAN
Smart battery UAVCAN bus
UAVCAN
BACKUP UAVCAN
Backup connectors
BACKUP UART
BACKUP AUX
Tracking beacon connector
Battery power connectors
ESC connecotrs
BAT1 and BAT2 be placed on opposite sides of the aircraft. They should be connected in series with an external 14 AWG wire between PAD1 and PAD2.
Battery 1
Battery 2
See battery 1 note
Battery 3
CAN buses are terminated inside Cube orange
CAN2 -> Smart batteries UAVCAN network CAN1 -> GNSS module communication Serial3 -> Telemetry Serial4 -> Backup uart Serial5 -> beacon Serial1 -> payload Serial2 -> payload
Check this link for PX4 current and voltage sensing setup https://docs.px4.io/v1.12/en/config/battery.html
Max differential input voltage for INA169 is 0.5 V
Place C3 in case low pass filtering on the output needed
PAYLOAD
USB
Check if HIROSE connector is the correct one
!VDD_BRICK_VALID
VDD_BRICK_VALID should be pulled low to make PX4 measure battery voltage and current

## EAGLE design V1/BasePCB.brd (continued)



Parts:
C2, C37, C55: 0.1uF; C0603; VOLTAGE 50V; LCSC# C14663
C11, C12, C13, C38, C39, C40, C56, C57, C58: 2.2uF; C1210; VOLTAGE 100V; LCSC# C55151
C14, C41, C59: 4700pF; C0603; VOLTAGE 50V; LCSC# C53987
C15, C42: 47pF; C0603; VOLTAGE 50V; LCSC# C1671
C16, C17, C18: 22uF; C2220; VOLTAGE 50V; LCSC# C784103
C43, C44, C45, C61, C62, C63: 47uF; C1210; VOLTAGE 25V; LCSC# C90142
C60: 47pF; C0603; VOLTAGE 50V; LCSC# C1620
D2, D5, D7: B560C; DO-214AB(SMC)
IC2, IC5, IC7: TPS54560B; SOIC8-POWERPAD
L4: 22µH; MWSA1206S
L5, L7: 7.2uH; 1064
LED1, LED2, LED3: LED-0603; LED0603; LCSC# C2286
PAD13, PAD14, PAD15, PAD16, PAD17, PAD18: PAD-S_2X2; 2х2
R5, R6: DNP; R0603
R7: 3K3; R0603; LCSC# C22978
R8: 7K5; R0603; LCSC# C23234
R9, R27, R39: 243K; R0603; LCSC# C23351
R10, R28, R40: 16K; R0603; LCSC# C4210
R11, R41: 143K; R0603; LCSC# C22877
R12, R17, R30, R42: 10K2; R0603; LCSC# C22772
R16: 1K; R0603; LCSC# C21190
R29: 53K6; R0603; LCSC# C23074
SJ1: SOLDER_JOINT-SJ1; RES_0

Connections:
GND: C11.1, C12.1, C13.1, C14.1, C15.1, C16.P$1 (1), C17.P$1 (1), C18.P$1 (1), C38.1, C39.1, C40.1, C41.1, C42.1, C43.1, C44.1, C45.1, C56.1, C57.1, C58.1, C59.1, C60.1, C61.1, C62.1, C63.1, D2.A, D5.A, D7.A, IC2.7 (GND), IC2.P$1 (GND), IC5.7 (GND), IC5.P$1 (GND), IC7.7 (GND), IC7.P$1 (GND), LED1.C, LED2.C, LED3.C, PAD13.P$1, PAD16.P$1, PAD18.P$1, R9.1, R12.1, R17.1, R27.1, R30.1, R39.1, R42.1; also elsewhere on the board
IO-CH7-PROT/24V_EN: R6.1; also elsewhere on the board
IO-CH8-PROT/12V_EN: R5.1; also elsewhere on the board
unnamed: C43.2, C44.2, C45.2, L5.2, PAD14.P$1, R29.2, SJ1.1
unnamed: IC7.3 (EN), R5.2
unnamed: C2.1, IC2.1 (BOOT)
unnamed: C2.2, D2.C, IC2.8 (SW), L4.1
unnamed: IC2.4 (RT/CLK), R9.2
unnamed: IC2.3 (EN), R6.2
unnamed: C15.2, IC2.6 (COMP), R10.2
unnamed: C14.2, R10.1
unnamed: IC2.5 (FB), R11.1, R12.2, R17.2
unnamed: LED1.A, R7.2
unnamed: LED2.A, R8.2
unnamed: LED3.A, R16.2
unnamed: C37.1, IC5.1 (BOOT)
unnamed: C37.2, D5.C, IC5.8 (SW), L5.1
unnamed: IC5.4 (RT/CLK), R27.2
unnamed: C42.2, IC5.6 (COMP), R28.2
unnamed: C41.2, R28.1
unnamed: IC5.5 (FB), R29.1, R30.2
unnamed: C55.1, IC7.1 (BOOT)
unnamed: C55.2, D7.C, IC7.8 (SW), L7.1
unnamed: IC7.4 (RT/CLK), R39.2
unnamed: C60.2, IC7.6 (COMP), R40.2
unnamed: C59.2, R40.1
unnamed: IC7.5 (FB), R41.1, R42.2
VDC: C11.2, C12.2, C13.2, C38.2, C39.2, C40.2, C56.2, C57.2, C58.2, IC2.2 (VIN), IC5.2 (VIN), IC7.2 (VIN); also elsewhere on the board
VDD_5V: R16.1, SJ1.2; also elsewhere on the board
VDD_12V: C61.2, C62.2, C63.2, L7.2, PAD15.P$1, R7.1, R41.2; also elsewhere on the board
VDD_24V: C16.P$2 (2), C17.P$2 (2), C18.P$2 (2), L4.2, PAD17.P$1, R8.1, R11.2; also elsewhere on the board

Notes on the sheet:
5V and 12V schematics are basically TI EVB module. Details here: https://www.ti.com/lit/ug/slvu863/slvu863.pdf?ts=1655463925178 24V schematic is based on webench simulator https://webench.ti.com/appinfo/webench/scripts/SDP.cgi?ID=FD50D1EF4279ADDB
Possible alternate inductor for 5V and 12 V DC-DC converters MWSA1004S-8R2MT from Sunlord
5V power source
12V power source
24V power source
SJ1 should be closed after output voltage check
Use testpad to check output voltage
When EN is left floating TPS54560 is enabled
R17 is here to keep BoM positions count low
L4 may be replaced with SRP1265A-220M from Bourns



Board: 4 copper layers, 175.9 x 141.0 mm, 132 parts (8 on the bottom side), 85 nets.

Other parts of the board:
U$1: AERODYNE
U$2: AERODYNE_SMALL

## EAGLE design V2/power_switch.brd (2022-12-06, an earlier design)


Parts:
CON1, CON2: CON-4P-TABS-JST-GH-TOP; BM04B-GHS-TB
CON3: CON-1P-XT150-FEMALE-PIN; XT150-FEMALE-PIN
CON4: CON-1P-XT150-MALE-PIN; XT150-MALE-PIN
D1, D2, D3, D4: SMBJ51CA-SMB; DO-214AA(SMB)
PAD1, PAD2, PAD3, PAD4, PAD5, PAD6, PAD7: PAD-5X8; 5X8
Q1, Q2, Q3, Q4: IRFR2407PBF; D-PAK
R1, R2, R3, R6: 100R; R0805
R4: 10K; R0805
R5: 24K; R0805
ZD1, ZD2, ZD3, ZD4: MM3Z11V; SOD323

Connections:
BATNEG: CON1.4, CON3.P$1, D1.A, D2.A, D3.A, D4.A, PAD2.P$1, PAD3.P$1, Q1.S, Q2.S, Q3.S, Q4.S, R4.2, ZD1.A, ZD2.A, ZD3.A, ZD4.A
BAT_POSITIVE: CON4.P$1, PAD1.P$1, PAD7.P$1
GATE: CON1.2, R1.1, R2.1, R3.1, R4.1, R5.2, R6.1
unnamed: Q2.G, R2.2, ZD2.C
unnamed: Q3.G, R3.2, ZD1.C
unnamed: Q1.G, R1.2, ZD3.C
unnamed: Q4.G, R6.2, ZD4.C
SYSTEM_GND: D1.C, D2.C, D3.C, D4.C, PAD4.P$1, PAD5.P$1, PAD6.P$1, Q1.D, Q2.D, Q3.D, Q4.D
VDC: CON1.1, CON2.1, CON2.2, R5.1

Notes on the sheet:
This comes from the PDB
This is external button connector



Board: 2 copper layers, 70.5 x 61.9 mm, 29 parts (5 on the bottom side), 9 nets.

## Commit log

2022-12-02 initial import
    [4portHub.brd, 4portHub.sch, 5portHub.brd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]
2022-12-02 manf docs import
    [BasePCB.brd]
2022-12-06 readme update
    [power_switch.brd, power_switch.sch]
2022-12-19 V3 import
    [BasePCB.brd, BasePCB.sch, LogicPCB.brd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]
2022-12-20 updates for V3
    [LogicPCB.brd, LogicPCB.sch, PowerPCB.brd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]
2022-12-20 silkscreen updates
    [LogicPCB.brd, LogicPCB.sch, PowerPCB.brd]
2022-12-23 V3.1 initial import
    [LogicPCB.brd, LogicPCB.sch, PowerPCB.brd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]
2022-12-23 V3 finalization
    [LogicPCB.brd, LogicPCB.sch, PowerPCB.brd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]
2022-12-23 V3 finished
    [LogicPCB.brd, LogicPCB.sch]
2022-12-23 link leds added
    [LogicPCB.brd, LogicPCB.sch]
2022-12-26 attribute updates
    [LogicPCB.brd, LogicPCB.sch]
2022-12-26 Payload connector replaced with 2 6-pin ones
    [LogicPCB.brd, LogicPCB.sch]
2022-12-27 InterPCB connectors issues fix
    [LogicPCB.brd, LogicPCB.sch, PowerPCB_mk0.brd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]
2022-12-27 silk updates
    [LogicPCB.brd, PowerPCB_mk0.brd, PowerPCB_mk0.sch]
2022-12-28 Minor fixes here and there
    [LogicPCB.brd, LogicPCB.sch, PowerPCB_mk0.brd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]
2022-12-30 PowerPCB updated for compatibility with rezonit requerements
    [PowerPCB_mk0.brd, PowerPCB_mk0.sch]
